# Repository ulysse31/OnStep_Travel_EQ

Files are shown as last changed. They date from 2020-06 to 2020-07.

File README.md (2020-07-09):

# 3D Printed Travel EQ

### Status : Beta / Work In Progress

3D Printed Motorised Traveling Equatorial mount compatible with OnStep eletronics Project.

The goal is to build a basic, simple, easy to transport EQ mount.

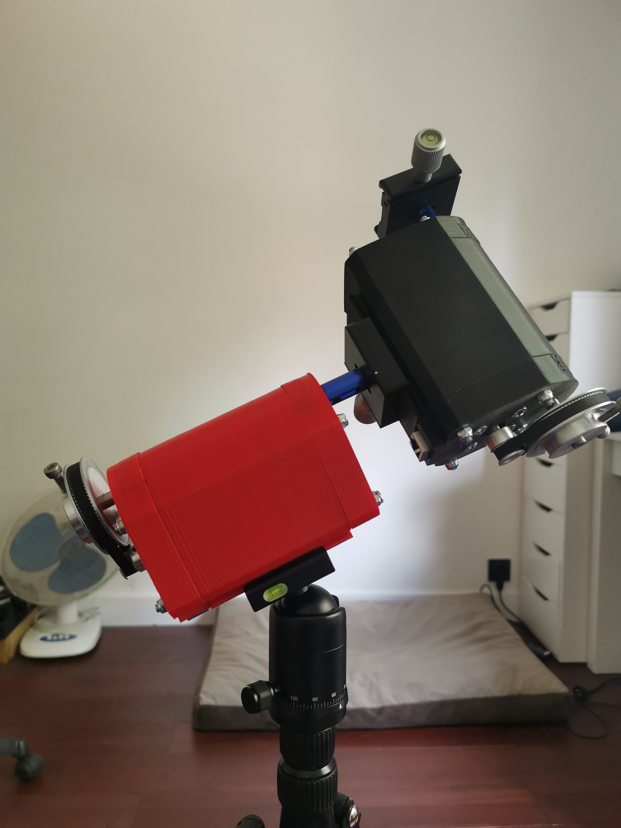
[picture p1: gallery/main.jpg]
Travel EQ Image


# What you need (Part list):
My travel EQ mount is composed of:
- The three 3D printed parts of this project (printed twice for DEC and RA so 6 total ^^')
- 2x NEMA17 motors (mine 400 steps, 47mm long nema17).
- 2x 100:1 gearbox (I used a OKD42 100:1 precision gearbox).
- 2x 80T GT2 pulley.
- 2x 20T GT2 pulley.
- 2x 92T (184mm) GT2 belt.
- 4x KFL08 bearings.
- 2x M8 steel tube (for now).
- M5 threaded rods (cut to length).
- M4 threaded rods (cut to length).
- 16x M5 locking nuts.
- 8x M4 locking nuts.
- 2x M5 to M8 shaft couplers (for now).
- 2x M5 to 1/4" adapter (for now).
- 2x RJ45 ports.
- 2x piece of copper PCB for etching the little boards for the RJ45 ports connectors.
- 4x M5 DIN912 screws for "easy" lock / unlock of the main axis.
- 2x Arca Swiss Quick & Release plates.
- A good photo tripod that can handle the load.

You can use other parts, but you'll have to modify the SCAD and regenerate the STLs.

On the elements marked "for now", this is because it is a beta version, I want to improve it and change those elements in the future.

# Precision :
With minimal 32 microsteps motor drivers, the 100:1 gearbox with 4:1 pulley/belt reduction, it should give arround 0.253 sec arc for tracking resolution.

# What you need to know :
- STL are made with some print gap, that may depend on your printer, you can modify it editing the SCAD and changing the "print_gap" value. Once modified, re-generate the three STL files for each blocks with OpenSCAD.
- If you want to customize it, please note that this design does NOT have a belt tensioner.
- This means the three 3D printed parts are made (customized in the SCAD file) to "fit" the exact size needed to tension the belt. Why didn't I put a belt tensioning system ? I wanted to keep it simple, and didn't find a "good and simple" way to add it to the design.
- Once printed, you'll have to sand a bit the interior to get the gearbox+motor inside the middle block. DO NOT FORCE TOO MUCH or you'll get stuck ^^'

Please keep in mind that this is a "Work in Progress" project, didn't even made "real life tests" for now.

# Things I would like to do on it in the future :
- Get rid of the shaft couplers by using 8mm tube with 5mm or 6mm inside threading
- Modelize a holder for a polaris scope / aligner, that could integrate this design and be easy to use.

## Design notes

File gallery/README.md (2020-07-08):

# Gallery

## Inside a block
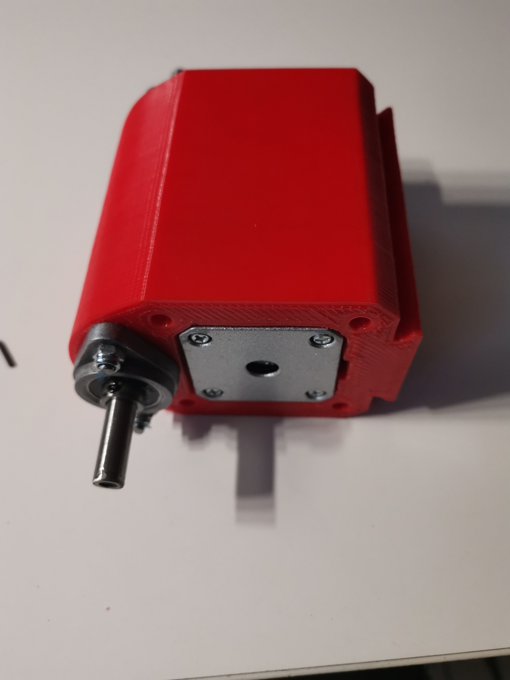
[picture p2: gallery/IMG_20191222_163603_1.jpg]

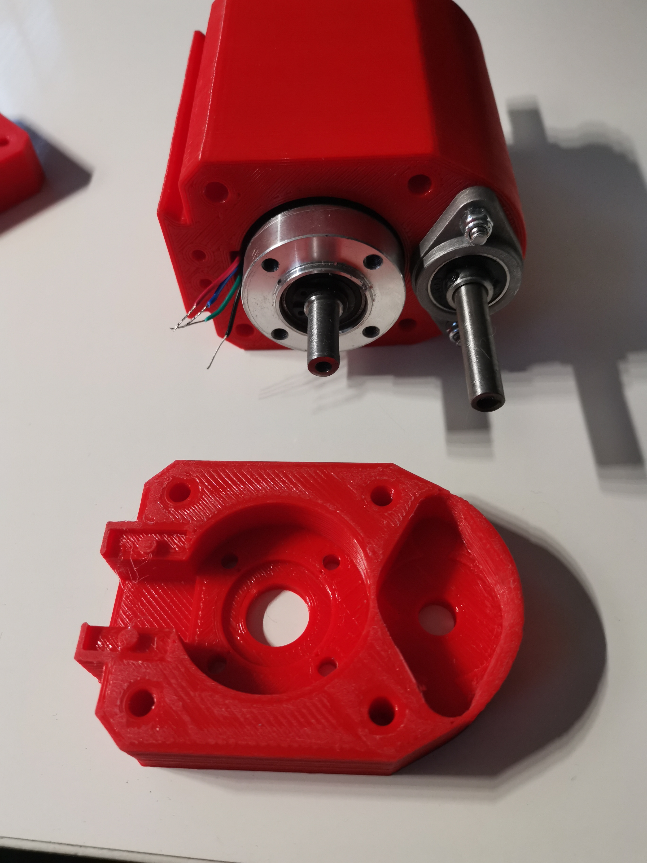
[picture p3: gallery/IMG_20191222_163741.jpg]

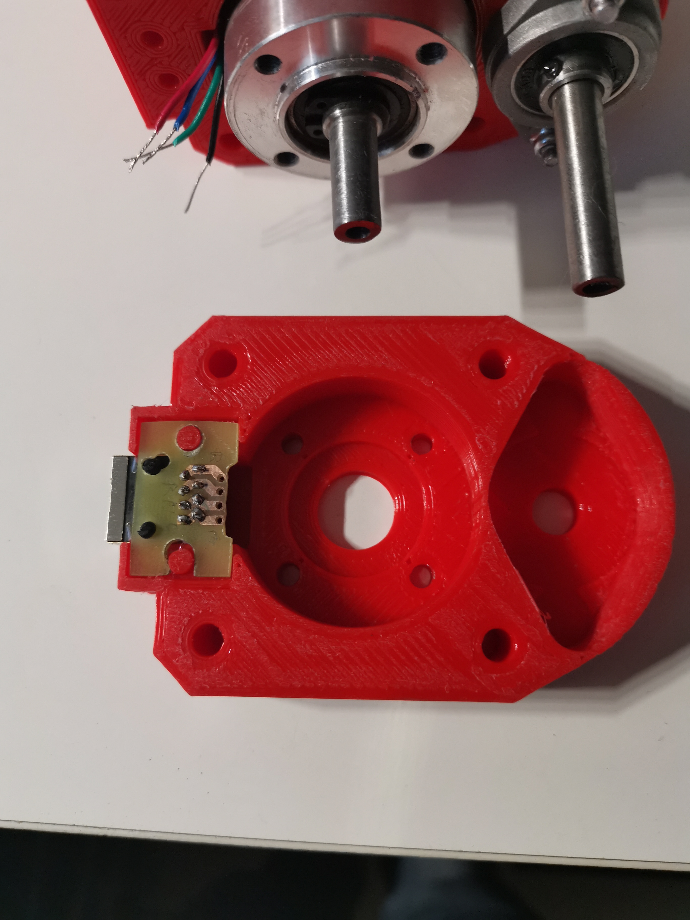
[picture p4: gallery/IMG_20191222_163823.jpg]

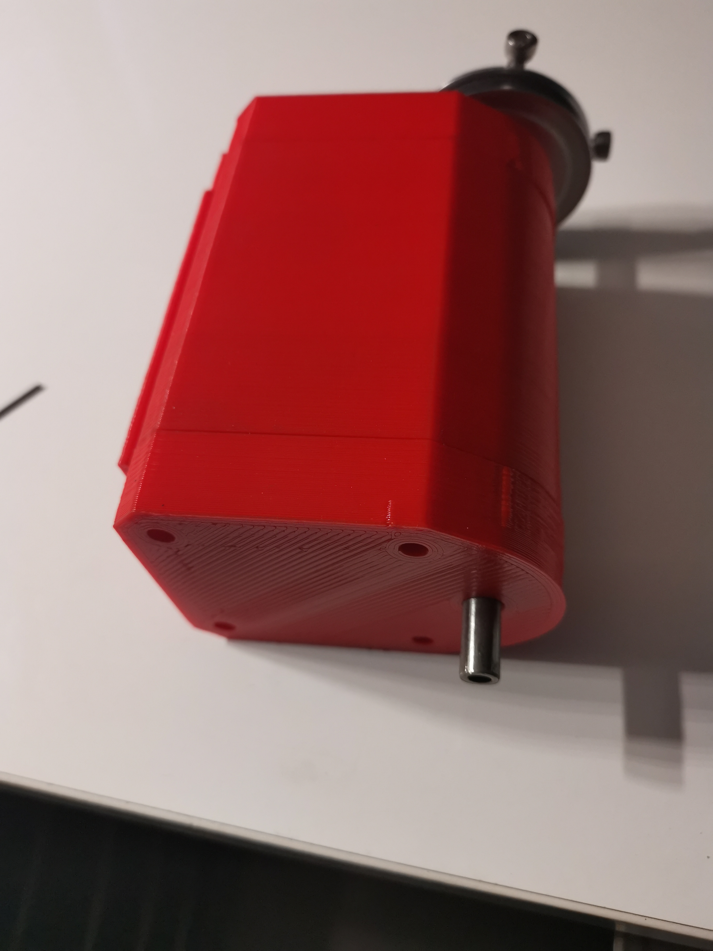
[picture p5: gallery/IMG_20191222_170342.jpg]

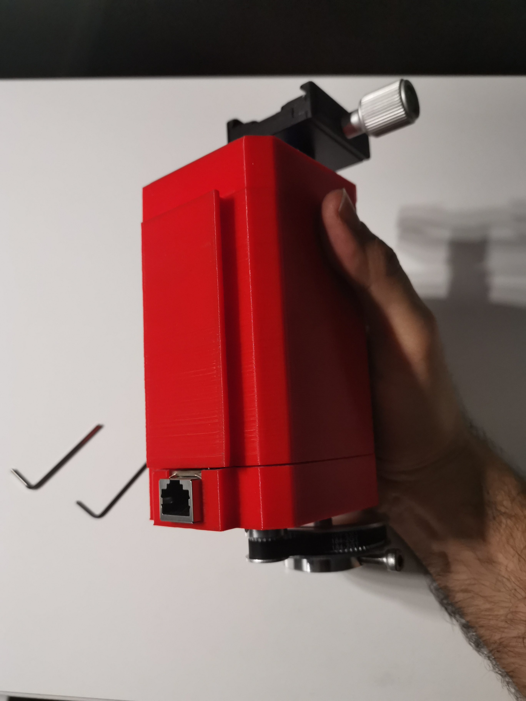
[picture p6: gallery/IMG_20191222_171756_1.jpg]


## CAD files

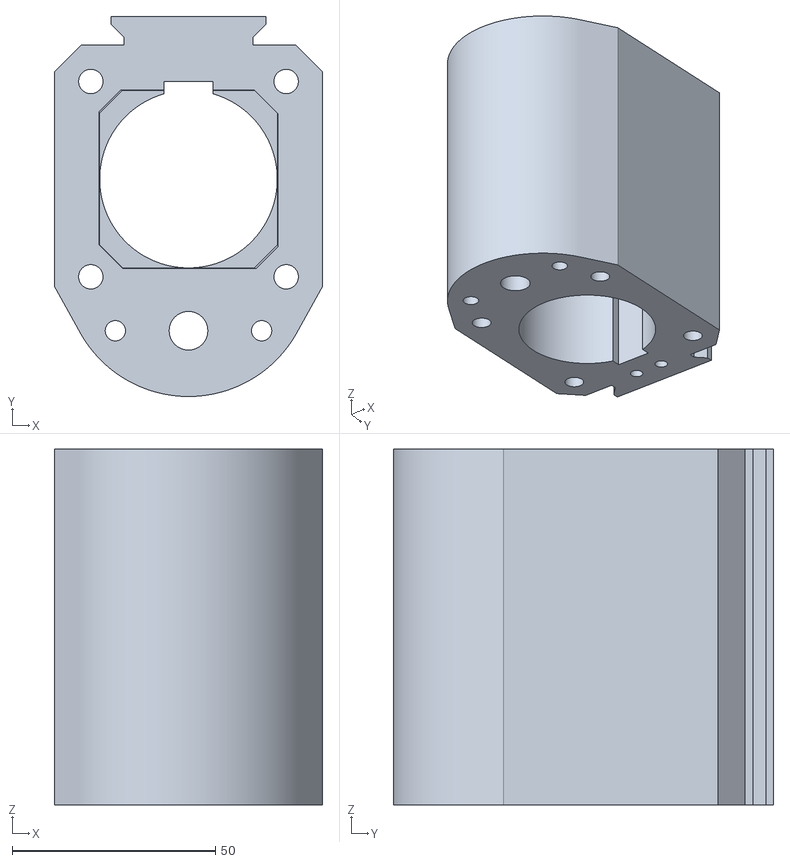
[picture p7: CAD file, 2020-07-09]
EQBlockMiddle.stl
66.0 x 93.5 x 87.5

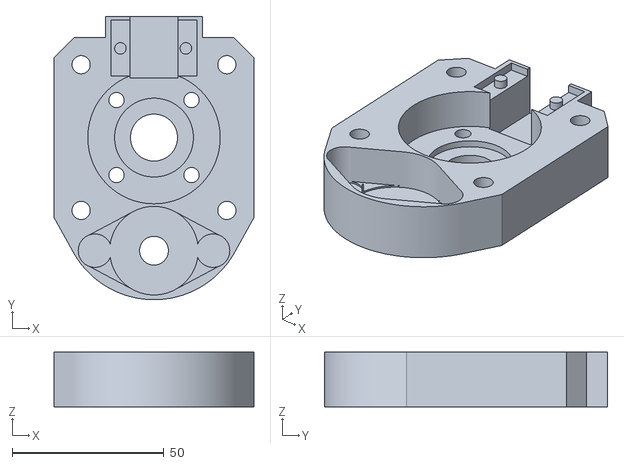
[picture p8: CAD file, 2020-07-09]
EQBlockBottom.stl
66.0 x 93.5 x 18.0

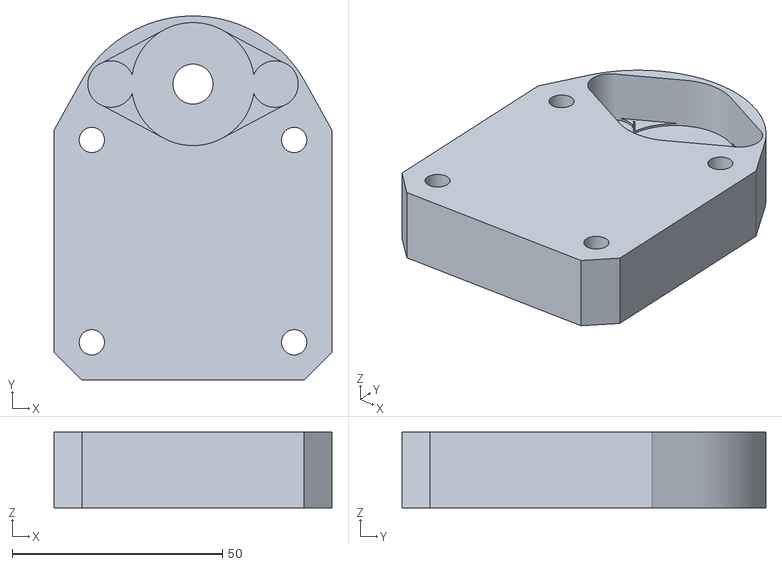
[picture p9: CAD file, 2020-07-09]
EQBlockTop.stl
66.0 x 86.5 x 18.0

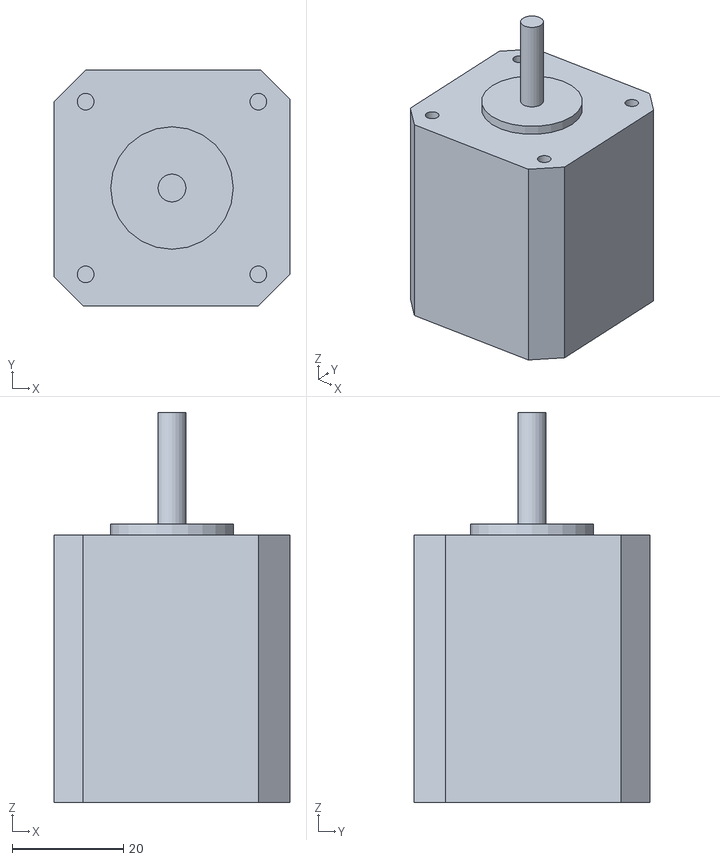
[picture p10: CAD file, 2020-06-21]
Nema17_48h.stl
42.3 x 42.3 x 70.0

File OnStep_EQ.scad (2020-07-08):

// 3D printed *Generic* Travel EQ mount for Onstep integration / usage
// Copyright (C) 2020  Victor do Vale, ulysse31@gmail.com a.k.a Nix
//
//This program is free software; you can redistribute it and/or
//modify it under the terms of the GNU General Public License
//as published by the Free Software Foundation; either version 2
//of the License, or (at your option) any later version.
//
//This program is distributed in the hope that it will be useful,
//but WITHOUT ANY WARRANTY; without even the implied warranty of
//MERCHANTABILITY or FITNESS FOR A PARTICULAR PURPOSE.  See the
//GNU General Public License for more details.
//
//You should have received a copy of the GNU General Public License
//along with this program; if not, write to the Free Software
//Foundation, Inc., 51 Franklin Street, Fifth Floor, Boston, MA  02110-1301, USA.
//
// Author :
// Victor do Vale (Ulysse31, a.k.a Nix) (ulysse31@gmail.com)
// 
//


// rendering variable : do not touch
$fn=300;



//
// BEGIN OF ADAPTATION VARIABLES
// HERE YOU CAN ADAPT TO YOUR PARTS THE 3D MODELS
// BY CHANGING THE SIZE AND VALUES
// I ADDED SOME COMMENTS TO HELP UNDERSTANDING EACH ONE
// ONCE EDITED GO TO END OF FILE TO UNCOMMENT THE DESIRED PART YOU WISH TO RENDER
// FOR STL GENERATION AND 3D PRINTING (printable_* functions)
//

// w_th : wall thickness, default 12mm
w_th=12;

// print_gap : gap for 3D printer overfill compensation => this depends on your printer, for me, its 2 mm (1 on each side)
print_gap=2;

//nema17_size : nema 17 "standard" size => if you wish to use nema23 ... change this ? (not tested ^^')
nema17_size=42;

// nema_hole_dist : distance of nema holes from center axis, 21.920310216782973 for nema17
nema_hole_dist=21.920310216782973;
// nema_hole_dia : diameter of nema screw holes
nema_hole_dia=3;

// gear_hole_dist : distance of the 4 gearbox top holes from the gearbox center axis, that screws to the top part 
gear_hole_dist=35/2;
// diameter of holes for nema fixation (aesthetical / 3d rendering visualization value)
gear_hole_dia=5;

// axis_pulley_dist : distance between the main axis, and the motor axis, center to center, this depends of your pulley sizes and belt type
// IT ALSO DEPENDS ON THE MANUFACTURER : some "adaptations" must be done depending of your hardware, I left here different value to give you a scenario 
// 184mm GT2 => here, this value was the "calculated one"
//axis_pulley_dist=36.94;
// corrected value mesured apon reception of belts & pulleys (bad idea, caliper not enough precise or human error ... arg...)
//axis_pulley_dist=36.82;
// re-mesured after first print (had to reprint)
// that value was the correct one FOR ME (and my parts)
axis_pulley_dist=37.32;

// axis_dia: axis diameter (8mm) but added a print gap of 1.5 (and code adds even more afterwords ... oh well ... at least it works ... :p )
axis_dia=9.5;

// MY KFL08 dimensions : depends on manufacturer => I strongly advise to wait reception and mesure BEFORE
// (some sellers gives bad/incorrect datasheets : I tested it myself :/ ...)
// height
KFL08_h=12;
// length
KFL08_l=48;
// width
KFL08_w=27;

// nema length/height used, mine : 47mm (46.5 from caliper).
nema_h=46.5;
// this is the height of my gearbox (OKD42 100:1 gearbox from ebay)
OKD42_h=53;

// RJ45 connector dimension used
rj45_x=15;
rj45_y=13;
rj45_z=18;

//
// END OF ADAPTATION PART
// DO NOT EDIT CODE BELOW, UNLESS YOU KNOW WHAT YOU ARE DOING
// THE ONLY PART INTERRESTING FOR "NON CODERS/MODELERS" IS AT THE END OF FILE
//


// Calculated size for middle block ...
eqblockDEC1_h=nema_h+OKD42_h-KFL08_h;

//
// GENERIC 3D functions
// 
module rotate_at(rotation, coord) {
  translate(coord)
    rotate(rotation)
    translate(-coord)
    children();
}


// this function modelize my gearbox (used for carving the parts).
module planetary_gearbox_OKD42(len, with_holes=0) {
  plate_h=5;
  cyl_r=21;
  cshaft_l=2;
  cshaft_r=12.5;
  shaft_r=4;
  shaft_l=21.6;

  difference()
    {
      union()
      {	
	difference()
	  {
	    translate([0, 0, plate_h/2]) cube([42, 42, plate_h], center=true);
	    union()
	    {
	      for (a=[45,135,225, 315])
		rotate([0, 0, a]) translate([0, 29.69, 3]) cube([10, 7.6, 10], center=true);
	    }
	  }
// 	translate([0, 0, plate_h/2]) cylinder(r=cyl_r,  h=len);
// 	translate([0, 0, plate_h/2+len]) cylinder(r=cshaft_r,  h=cshaft_l);
// 	translate([0, 0, plate_h/2+len+cshaft_l]) cylinder(r=shaft_r,  h=shaft_l);

	translate([0, 0, 0]) cylinder(r=cyl_r,  h=len);
	translate([0, 0, len]) cylinder(r=cshaft_r,  h=cshaft_l);
	translate([0, 0, len+cshaft_l]) cylinder(r=shaft_r,  h=shaft_l);

      }
	union()
	{
	  if (with_holes==1)
	    {
	      for (a=[45, 135, 225, 315])
		{
		  rotate([0, 0, a]) translate([0, nema_hole_dist, -0.01]) cylinder(r=nema_hole_dia/2, h=plate_h+0.02);
		  rotate([0, 0, a]) translate([0, nema_hole_dist, plate_h/2]) cylinder(r=nema_hole_dia, h=plate_h+plate_h/2+0.02);
		  rotate([0, 0, a]) translate([0, gear_hole_dist, len-plate_h*2]) cylinder(r=gear_hole_dia/2, h=plate_h+len+0.02);
		}
	    }
	}
    }
}

// generic function that is later called to carve the parts (change content if you code your own gearbox module)
module planetary_gearbox(len, with_holes=0)
{
  planetary_gearbox_OKD42(len, with_holes);
}

// Imports a 3d model of a nema17 (for carving/3d rendering)
module nema17_geared(gearlen,with_holes=0) {
  import("./Nema17_48h.stl");
    if (with_holes == 0)
    {
      // renoving nema stl holings ...
      for (a=[45, 135, 225, 315])
	{
	  rotate([0, 0, a]) translate([0, nema_hole_dist, nema_h-12-0.01]) cylinder(r=nema_hole_dia/2+1, h=12+0.02);
	  //rotate([0, 0, a]) translate([0, nema_hole_dist, plate_h/2]) cylinder(r=nema_hole_dia, h=plate_h+plate_h/2+0.02);
	  //	  rotate([0, 0, a]) translate([0, gear_hole_dist, len-plate_h*2]) cylinder(r=gear_hole_dia/2, h=plate_h+len+0.02);
	}
    }
  translate([0, 0, nema_h]) planetary_gearbox(gearlen, with_holes);
}

module nema17() {
  import("./Nema17_48h.stl");
}


module EQBlockDECbottom()
{
  top_h=18;
  //  translate([nema23_hole_dist/2, nema23_hole_dist/2, 0]) cylinder(r=3, h=130);
  echo("eqblockDEC1_h=",top_h);
  difference()
    {
      union()
      {
	difference()
	  {
	    union()
	    {
	      translate([-nema17_size/2-w_th, -nema17_size/2-w_th, 0]) cube([nema17_size+w_th*2, nema17_size+w_th*2, top_h]);
	      translate([0, (nema17_size+w_th)/2-4, 0]) cylinder(r=(nema17_size+w_th+7)/2, h=top_h);
	      translate([-(rj45_x+16.9)/2, -nema17_size/2-1, -0.01]) rotate([90,0,0]) cube([rj45_x+16.9,top_h,rj45_z+0.02]);
	      //	      translate([0, (nema17_size+w_th)/2, 0]) cylinder(r=(nema17_size+w_th)/2, h=top_h);
	    }
	    union()
	    {
	      for (a=[45, 135, 225, 315])
		  rotate([0, 0, a]) translate([0, 34,-0.01]) cylinder(r=3, h=top_h+w_th+20);
	      for (a=[45, 135, 225, 315])
		  rotate([0, 0, a]) translate([-4.75, 42,-0.01]) cube([9.5,9.5,top_h+w_th+20]);
	    }
	  }
	//	translate([0, (nema17_size+w_th)/2-1, 0]) cylinder(r=(nema17_size+w_th+4)/2, h=top_h);
	rotate_at([0,0, 29.05], [nema17_size/2+w_th, nema17_size/2+5.4, 0]) translate([nema17_size/2+w_th-5, nema17_size/2+5.4, 0]) cube([5,13, top_h]);
	rotate_at([0,0, -29.05], [-nema17_size/2-w_th, nema17_size/2+5.4, 0]) translate([-nema17_size/2-w_th, nema17_size/2+5.4, 0]) cube([5,13, top_h]);
      }
      union()
      {
	translate([0, 0, -0.01-print_gap]) cylinder(r=axis_dia/2+3, h=nema_h+OKD42_h+w_th*2+0.02);
	translate([0, axis_pulley_dist, -0.01-print_gap]) cylinder(r=axis_dia/2, h=nema_h+OKD42_h+w_th*2+0.02);
	translate([0, axis_pulley_dist, -0.01-print_gap]) resize([KFL08_l+print_gap,0,0], auto=true) KFL08(5);
	translate([0, 0, -0.01-eqblockDEC1_h-1.7-print_gap]) resize([nema17_size+print_gap,0,0], auto=true) nema17_geared(OKD42_h);
	for (a=[45, 135, 225, 315])
	  rotate([0, 0, a]) translate([0, gear_hole_dist, 0]) cylinder(r=gear_hole_dia/2, h=top_h+0.02);
	//translate([-5, -nema17_size/2-5, -0.01]) cube([10,4,top_h+0.02]);
	translate([-rj45_x/2-0.5, -nema17_size/2+1.3-0.01, -0.02]) rotate([90,0,0]) cube([rj45_x+1,rj45_y+3,rj45_z+5+0.02]);
	translate([-(28.5/2), -nema17_size+3.2-0.02, -0.02]) 
	  {
	    difference()
	      {
		cube([28.5,18.5, 2.5]);
		union()
		{
		  translate([3.17, 8.89+0.5, -0.02]) cylinder(r=1.91, h=3);
		  translate([24.77, 8.89+0.5, -0.02]) cylinder(r=1.91, h=3);
		}
	      }
	  }
      }
    }
  //  translate([-rj45_x/2, -nema17_size/2-1-0.01, 1.6]) rotate([90,0,0]) cube([rj45_x,rj45_y,rj45_z]);
}


module EQBlockDECtop()
{
  top_h=18;
  echo("eqblockDEC1_h=",top_h);
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

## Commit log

2020-07-08 added simulation module to simulate the entire structure (module/function showcase)
    [OnStep_EQ.scad]
2020-07-08 added code / variables comments added GPLv2 licensing
    [OnStep_EQ.scad]
2020-07-08 Delete 15T-GT2.stl
    Used for 3d visual representation, not used anymore
    [15T-GT2.stl]
2020-07-08 Delete parametricPulley_v3-15T.scad
    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
    [parametricPulley_v3-15T.scad]
2020-07-08 Delete parametricPulley_v3-60T.scad
    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
    [parametricPulley_v3-60T.scad]
2020-07-08 Delete parametricPulley_v3.scad
    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
    [parametricPulley_v3.scad]
2020-07-08 Delete OnStep_EQ_bottom_testv2.stl
    3d printed slice of middle block just to check motor fit. not used anymore
    [OnStep_EQ_bottom_testv2.stl]
2020-07-09 cleaned a bit the scad file
    added default STL that fits my part list.
    [EQBlockBottom.stl, EQBlockMiddle.stl, EQBlockTop.stl]
